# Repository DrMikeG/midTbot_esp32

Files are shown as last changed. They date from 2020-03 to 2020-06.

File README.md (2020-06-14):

# MidTBot ESP32



The MidTBot is a small and simple little pen plotter. All of the custom parts are 3D printed. The rest of the parts are low cost and easy to get.

The controller uses an ESP32 running Grbl_ESP32 firmware. It can be controlled via USB, Bluetooth or Wifi. You can simply upload gcode files to the unboard SD card and print.

The machine is controlled by a unique H-bot configuration, that uses a single belt. Two small stepper motors drive that belt in a special way to move in the X/Y plane. The pen is lifted by a hobby servo using a very simple and accurate mechanism.

[Here is a link to a video of the plotter in action.](https://www.youtube.com/watch?v=jiwWCrCfXrY)

The project is open source (Creative commons 4.0 Attribution - Share Alike) and all the files are in this Githob repo. Assembly instructions [are here](https://github.com/bdring/midTbot_esp32/wiki/Assembly-Instructions). If you have questions, please ask them by opening an issue in this repo.

### Check it out on GrabCad

Click on image for interactive viewer in browser.

GrabCAD (https://workbench.grabcad.com/workbench/projects/gcj3zJAQexD3ve_8KkwymatyKXhCWnRs8TB5U1ojGxl3s4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)

### Kits

There currently are no full kits for sale. [Controller kits are available on Tindie](https://www.tindie.com/products/33366583/midtbot-esp32-v1-controller-kit/).

### Donation

This project represents a lot of work. Please consider a safe, secure and highly appreciated donation via the PayPal link below.



## 2020-02-21 ##

I've got the latest arduino ide updated
I've added the esp32 board manager as described here https://github.com/espressif/arduino-esp32/blob/master/docs/arduino-ide/boards_manager.md

I've not pulled the development repo of https://github.com/espressif/arduino-esp32 - hopefully I don't need to do that?

I've copied the libraries from grbl\libs as described here: https://github.com/bdring/Grbl_Esp32/wiki/Compiling-the-firmware
/Volumes/ExtData03_2TB/Users/mike/Documents/Arduino/libraries

I've set the board settings in Ardino IDE as described here: https://github.com/bdring/Grbl_Esp32/wiki/Compiling-the-firmware

I've opened /Volumes/ExtData03_2TB/Users/mike/arduino/Grbl_Esp32/Grbl_Esp32/Grbl_Esp32.ino and I'm  trying to compile

Compiled unchanged...

The file "cpu_map.h" contains pin maps for several common setups. The master configuration file "config.h" selects one of those pin maps via a "#define" line near the top of that file.

Trying to program CPU_MAP_TEST_DRIVE onto actual board...

Compiled board with test_drive and that seemed to work.
Can't catch IP address on serial, but did find wifi GRBL_ESP, with password 12345678.
(See https://github.com/bdring/Grbl_Esp32/wiki/ESP3D-Web-UI-for-Grbl_ESP32)

You can also get them by sending $I on a serial terminal.

Changed config.h to have:
#define CPU_MAP_MIDTBOT // these are defined in cpu_map.h
recompiled and flashed to board.

Connected to the wifi network. Uploaded index.html.gz from this repo.

Putting esp board onto controller board
(Micro usb slot points off the edge of the board)

Plugged in stepper motor nearest boards (X?) Used UI to Jog X - it moves...
Connected second stepper - they both move when you job X/Y - remember it's a H-bot.

Connected up the servo. Jogged Z. That moves ok too.

Need to remember to adjust the stepper power to get the right cooking temp....

# 28th Feb 2020 #

Final screws arrived so attached steppers to the main board.
Threaded belt. Booted.

Need to follow instructions for attaching servo horn.

## Setting up the motors ##

Set the trimpot to minimum to start with, by turning the trimpot fully anti-clockwise. Turn clockwise until the motors are not skipping steps at your target speed and load.

https://github.com/bdring/midTbot_esp32/wiki/Setting-Up-the-Motors

https://github.com/bdring/midTbot_esp32/wiki/Setting-Up-the-Motors#overview-1

Set $rst=$ to reset all of the default Grbl settings.
Check the status by sending the ? character.
It should report that there is an alarm. This is because you have not homed yet.
Send $X to clear the alarm

Send $X to clear the alarm. You then need to send some small test moves to check the direction. 
Send G91 to put it in (incremental distance mode). Next send G0X2 to move the X axis 2mm to the right. Send G0Y2 to move the Y axis 2mm back. If either of these go the wrong direction you have to rotate one or more of the motor connectors 180 degrees.

Send $H to home the machine.

I think the wiring was correct all along - I just had one or more of the stepper drivers dialled down too low for homing work.
I cleared the alarm with $X, turned both trim pots a fraction clock-wise and rehomed in Y and X. Seemed fine so powered down for tonight.

For my colour wires, the correct wiring colours away from the ESP board are RGBY/GPBW
Wrong! Today the correct colours are: RGBY/WBPG

## Setting the X,Y 0,0 point.##
Homing does not set a 0,0 point. You need to tell it where that is. 
Home is min(X),max(Y) (top left hand corner)
Typically you would want jog to the lower left point and the set the 0,0 there.
min(X),min(Y) (lower left hand corner)
After homing move the down in negative Y. Be sure you don't hit the limit of travel. If you do, re-home and try again. 
Once there, set the 0,0. There are also zeroing buttons near the jog panel in the GUI.

## Pen Servo Setup ##

// Required
$rst=#
$3=4 (reverse the Z direction) (Has this reversed X and Y?!)
$102=90 (short pen lower stroke)
G10L2P0Z-5 (Avoid grounding pen at home.)

G0Z5 is pen up.

Clear the homing alarm by sending $X over the serial port.
Next send $rst=#. This will reset any machine offsets that might be in memory.
Send G0Z5 the servo should move to one end of the travel.
You can see the other end of the travel by sending G0Z0.
Send G0Z5 again to move to the pen up position. The servo should be rotating clockwise to lift the pen and counterclockwise to lower it. 

I need to send $3=4 to reverse the Z direction
(Not all servos travel the same way. If yours is going the wrong way, send $3=4 to reverse the Z direction.)

With the machine at Z5, mount the servo horn in a position that holds up the pen lift part. You want it to be holding the pen up close to the max height, but there should be a little travel left.

Changing $102 (adjusts Z0) From default (100). Sending $102=90 add 10% towards Z5 (up))

Used G0Z0 to install pen

## Home and first draw ##
Using WebUI 

Jogged as far in -Y as I dare.
Not sure I hit the zeroing button in the UI? (It dropped the pen) 
G10L20P0X0Y0 

I've drawn to test drawings of midthead.gcode (both seem to finish with a long random line with the pend down?!)

Trying to debug random line on completion? 
https://ncviewer.com/ shows this isn't a g-line. It could either be the home command or part of the firmware?

Also homed X and Y independently from Z? This stopped the pen dropping.
Click the X and Y wheel cross not the co
## Process ##
[Position bad paper]
Power on
Connect to wifi (12345678)
$X (clear alarm)
G0Z0 (pen down)
[Fit pen]
G0Z5 (pen up)
G10L2P0Z-5 (Avoid grounding pen at home.)
[Position good paper]
Click home Y
Click home X
Move -Y by about -1000 to move to bottom left corner of range
Click zero X
Click zero Y
[Need to figure out drawing Csys from 0,0 process]
[Execute GCode to draw picture]

if gcode contains G28 you may wish to remove it? Just end on pen up!

## How to make GCode ##
https://youtu.be/bbe56S_O-uI

Open Inkscape
> Document Properties
>> Default UNITS mm
>> Units mm
>> Width 180 (plotter bed size)
>> Height 220 

Import image into inkscape
Scale
Goto path tab
> Trace bitmap
>> Update
>> Ok
>> Close
Delete image (keep path)
Select object, on path menu click on object to path
>> Path tab
>>> Dynamic offset

/Volumes/ExtData03_2TB/Users/mik

## Added inkscape MakerBot Unicorn G-Code extension ##

Test params:
50/30/150/150/1500/1000/0/0 

https://shopcraftables.com/free-svg-cut-files/?sort=featured&page=6

## Messing about ##

There are some scaling tricks in inkscape.
Display units must be px.
Page scale should be 1.0

The produced gcode has F speed tags. Which can be removed or changed.

# 7th March 2020

https://www.norwegiancreations.com/2015/08/an-intro-to-g-code-and-how-to-generate-it-using-inkscape/

Useful guide to the inkscape gcode plugin. Recomends visualising (including timings) in Camotics

I probably don't need a post processor if I change the settings in the green tool table.

Having scolded my Son repeatedly about running with his tablet, he sheepishly presented me with broken headphones.

Dodgy jack? Easy repair? Only got to solder three wires - easy!

Not when they are crappy, enameled strand twisted pairs in a stretchy yellow plastic sleeve.

I only recently learned you can tin enamelled ends by bubbling them in solder.

After three fails attempts to splice them end-to-end with no strain relief, I admitted default and soldered them back to back.
At least my Son has his headphones back for (home) school tomorrow.

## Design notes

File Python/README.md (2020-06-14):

# Python processing

https://confluence.atlassian.com/bitbucketserver/markdown-syntax-guide-776639995.html

## 7th May 2020 ##

Read the file line by line

My file contains two layers, which are represented as groups <g> tags - this allows me to compare the edited and unedited porition - although my clumbsy edited actually edits both sections, and I use cut and paste to 'fix' one to be unedited afterwards.

Paths look like this.
The m is move to, 
the little c means this is a relative, polybezier.
the z at the end means closed
there are a few with h or v in, which is something I don't copy with yet.

To start with, I just counted the , but smaller area paths can still have high complexity
Then I tried to count the maxium displacement - this worked ok, but favoured long thing over round areas
Then I tried to estimate the area, treating the coordinates as vertices - this works pretty well, but makes some mistakes I don't yet understand

I am going to try and do a better approximation.

Example from round_church

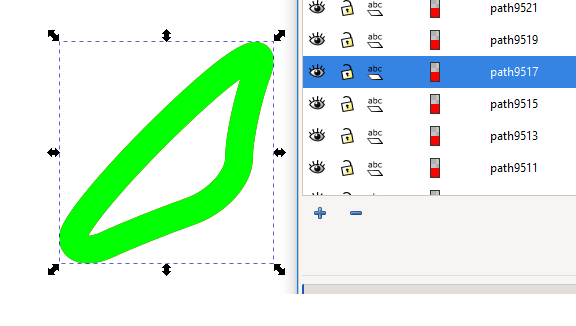
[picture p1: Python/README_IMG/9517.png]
Path 9517


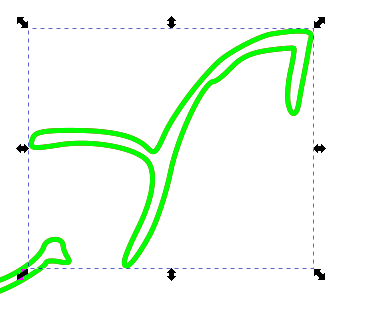
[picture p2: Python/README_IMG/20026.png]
Path 20026


<path
       style="fill:none;stroke:#ff0000;stroke-width:4.75441"
       d="m 4644.4095,-2548.3896 c 0,-3.5888
       5.4618,-17.2226
       12.1128,-30.2972 
       16.7193,-32.8657 
       19.9951,-59.5102 
       8.5584,-69.6047 
       -13.504,-11.9192 
       -53.5095,-18.6102 
       -83.053,-13.8908 
       -28.3172,4.5236 
       -30.4106,3.9963 -26.3313,-6.6333 2.1808,-5.684 10.6209,-7.3367 37.4652,-7.3367 38.9853,0 61.8412,5.1796 73.2651,16.6034 7.1663,7.1665 8.4357,6.2244 16.8068,-12.4727 8.8095,-19.6765 33.7221,-53.1188 52.8358,-70.926 10.1483,-9.4546 39.2933,-24.6833 50.9526,-26.6237 28.2093,-4.6946 40.3298,-3.7252 38.5725,3.0851 -1.0117,3.9224 -2.2978,10.3409 -2.8578,14.2633 -0.5601,3.9224 -2.5303,14.6198 -4.3793,23.7721 -1.8485,9.1522 -3.8882,20.3226 -4.5319,24.823 -1.9417,13.5655 -7.1421,15.0562 -10.1878,2.9204 -1.5756,-6.2776 -0.7303,-20.9135 1.8785,-32.5243 2.6087,-11.6108 4.1434,-21.7105 3.4103,-22.4436 -0.7331,-0.7332 -11.8451,0.1022 -24.6935,1.8561 -16.9475,2.3136 -26.8206,6.886 -35.9652,16.6559 -6.9329,7.4068 -14.5038,13.4669 -16.8244,13.4669 -10.009,0 -34.8409,51.7177 -42.2316,87.9566 -4.2666,20.9194 -13.2477,48.2348 -19.9581,60.7007 -13.6166,25.2942 -24.877,37.373 -24.8441,26.6495 z"
       id="path20026" />

https://www.w3.org/TR/SVG/paths.html

The cubic Bézier commands are as follows:

| Command | Name | Parameters | Description |
| --- | ----- | --- | --- |
| C (absolute) c (relative) | curveto | (x1 y1 x2 y2 x y)+ | Draws a cubic Bézier curve from the current point to (x,y) using (x1,y1) as the control point at the beginning of the curve and (x2,y2) as the control point at the end of the curve. C (uppercase) indicates that absolute coordinates will follow; c (lowercase) indicates that relative coordinates will follow. Multiple sets of coordinates may be specified to draw a polybézier. At the end of the command, the new current point becomes the final (x,y) coordinate pair used in the polybézier. |

This was invaluable https://medium.com/@adrian_cooney/bezier-interpolation-13b68563313a

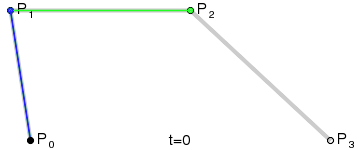
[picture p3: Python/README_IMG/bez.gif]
Cubic Bezier: How it work


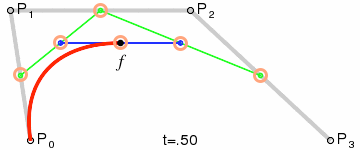
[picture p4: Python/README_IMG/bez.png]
Code for point at T


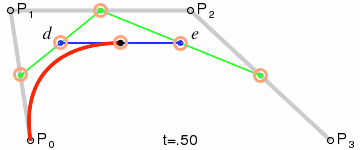
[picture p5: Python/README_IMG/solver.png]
solver


```
float T = 0.5;
CGPoint A = pointInLine(p0, p1, T);
CGPoint B = pointInLine(p1, p2, T);
CGPoint C = pointInLine(p2, p3, T);
CGPoint D = pointInLine(A, B, T);
CGPoint E = pointInLine(B, C, T);
CGPoint F = pointInLine(D, E, T); // The juicy one
```

4 pairs
start point, control point 1, control point 2 end point.
The curve passes though start and end point.

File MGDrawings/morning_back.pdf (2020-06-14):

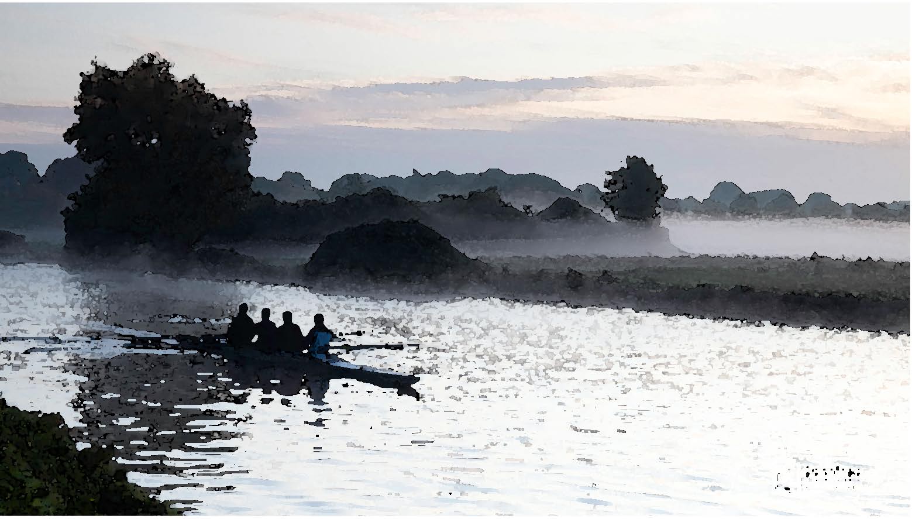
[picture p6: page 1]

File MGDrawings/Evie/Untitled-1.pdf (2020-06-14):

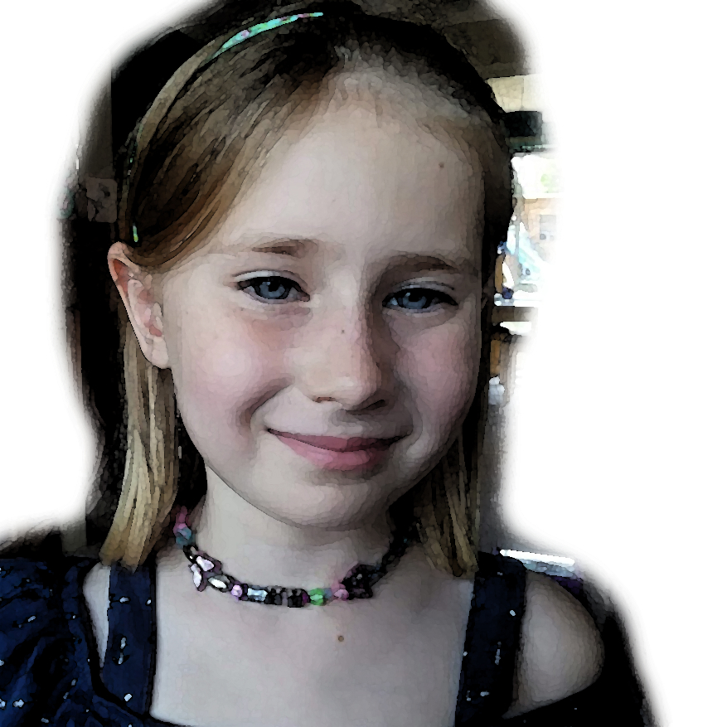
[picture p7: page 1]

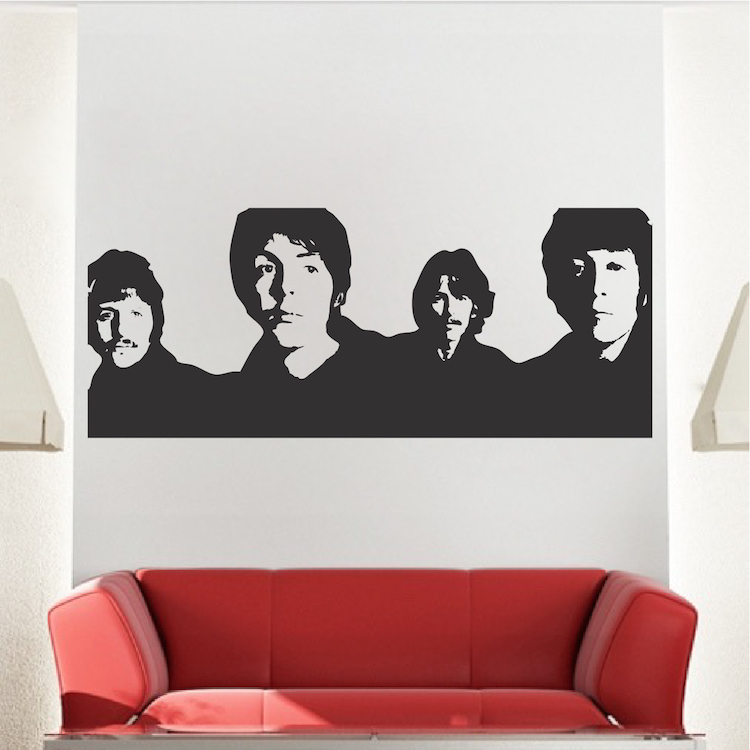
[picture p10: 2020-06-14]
MGDrawings/fab4/The_Beatles_Vinyl_Wall_Decal_Mural_Stickers_a87.jpg

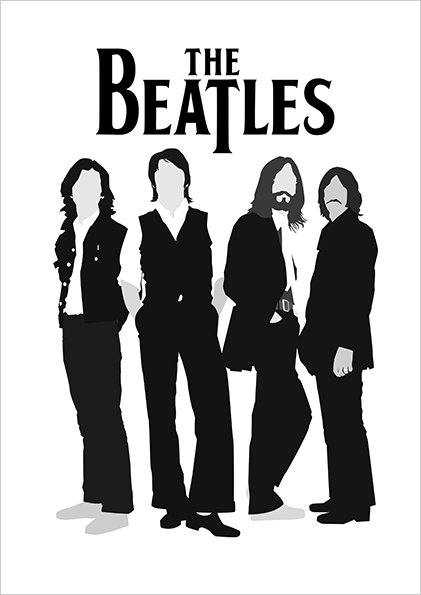
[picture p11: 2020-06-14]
MGDrawings/fab4/the-beatler1.png

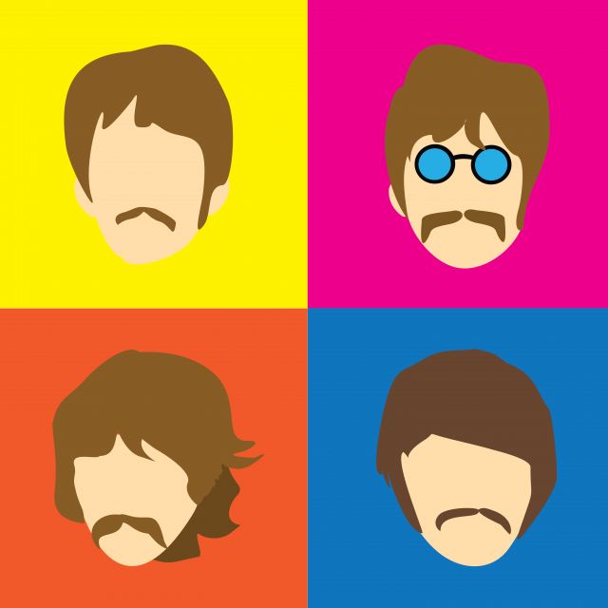
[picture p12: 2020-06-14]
MGDrawings/fab4/kPZz_WhzKAPGD-5CDNo-pWeygAgRfgy3-cropped-1x1-browser.jpg

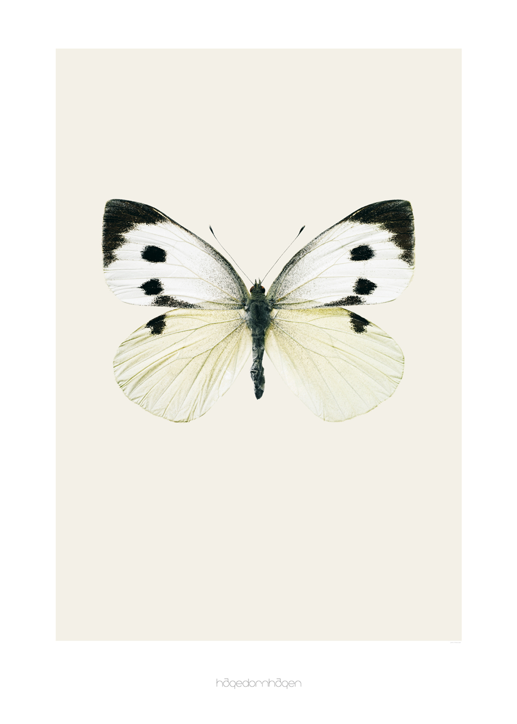
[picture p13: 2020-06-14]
MGDrawings/H-9.jpg

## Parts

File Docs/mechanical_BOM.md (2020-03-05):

### Mechanical Parts List

| Description | Qty  | Source | Help |
| --- | ---- | --- | --- |
| Carriage Block | 1 | 3D Printed |  Printed |
| Cover (optional) | 1 | 3D Printed |  Printed |
| Left Foot | 1 | 3D Printed |  Printed |
| Right Foot | 1 | 3D Printed |  Printed |
| Head Block | 1 | 3D Printed |  Printed |
| Tail Block | 1 | 3D Printed |  Printed |
| Pen Mounting Block | 1 | 3D Printed |  Printed |
| Linear Bearing Shaft 6mm Dia. x 200 lg. | 4 | [Amazon](<https://www.amazon.com/ReliaBot-inches-Hardened-Chrome-Plated/dp/B07R16DRVY>) |  Arrived |
| Linear Bearing LM6LUU (wide Style) | 4 | [Amazon](<https://www.amazon.com/uxcell-LM6LUU-6mmx12mmx35mm-Bushing-Bearing/dp/B01N3MO4FA>) | Arrived |
| Pulley GT2 16Tooth 6mm 5mm Shaft | 2 | [Amazon](<https://www.amazon.com/WINGONEER-Aluminum-Timing-Pulley-Printer/dp/B077YHJHVH>) |  5 Arrived |
| Smooth Idler Pulley 3mm I.D. 16Tooth Dia 13mm Flange Dia | 6 | [Amazon](<https://www.amazon.com/BALITENSEN-Smooth-Pulley-Toothless-Printer/dp/B077GXV7BJ>) | 10 Arrived [Issue](https://github.com/bdring/midTbot_esp32/issues/3) |
| Stepper Motor NEMA14 x 20mm Tall 5mm Shaft | 2 | [StepperOnLine](<https://www.omc-stepperonline.com/nema-14-stepper-motor/nema-14-bipolare-1-8deg-5ncm-7-08oz-in-0-4a-10v-35x35x20mm-4-fili.html>) |  2 Arrived [Issue](<https://github.com/bdring/midTbot_esp32/issues/10>) |
| GT2 6mm Wide Belt | 1m | [Amazon](<https://www.amazon.com/Mercurry-Meters-timing-Rostock-GT2-6mm/dp/B071K8HYB4>) | Arrived |
| Controller PCB | 1 | | Arrived |
| Button Screw M3 x 50mm | 1 | Ordered 2 Ebay (not arrived) Ordered 4 more from Kays (ebay) | |
| Hex Nut M3 Locking | 1 |  ordered 5 ebay |  arrived |
| Socket Head Screw M5 x 14 | 1 | ordered 5 ebay | arrived |
| Socket Head Screw M3 x 16 | 6 | ordered 10 ebay | arrived |
| Button Head Screw M3 x 8mm | 6 |  ordered 10 ebay (not arrived)  Ordered 10 more from Kays (6mm arrived - refunded) Order 10x10mm from Kays (ebay) | |
| Rubber Foot 1/2" dia x 1/8" Thk | 4 | [Amazon](<https://www.amazon.com/Self-Stick-Noise-Dampening-Bumpers-12-pieces/dp/B001WAK6DS>) | arrived |
| Bearing 3mm x 7mm x 3mm (683ZZ) | 2 | [Amazon](<https://www.amazon.com/gp/product/B00ZHSR2QU>) | Arrived |
| Hobby Servo MG90S | 1 | [Amazon](https://www.amazon.com/s?k=mg90) | Arrived |
| 12V 3A Power Supply | 1 | [Amazon](https://www.amazon.com/Adapter-100-240V-Transformers-Switching-Wireless/dp/B073WSWT34) |  In parts bin |

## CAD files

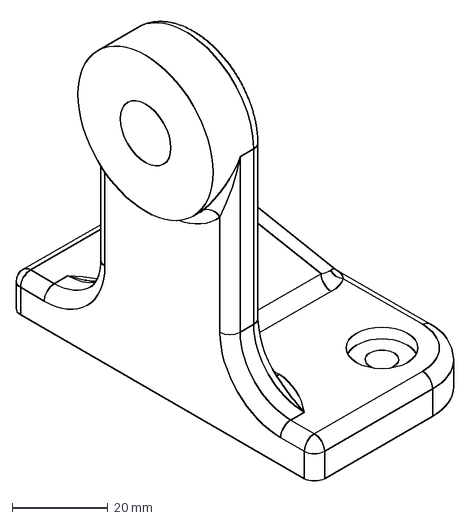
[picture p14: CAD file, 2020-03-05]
MGDrawings/New Stand_v20.dxf
91.5 x 97.3 mm

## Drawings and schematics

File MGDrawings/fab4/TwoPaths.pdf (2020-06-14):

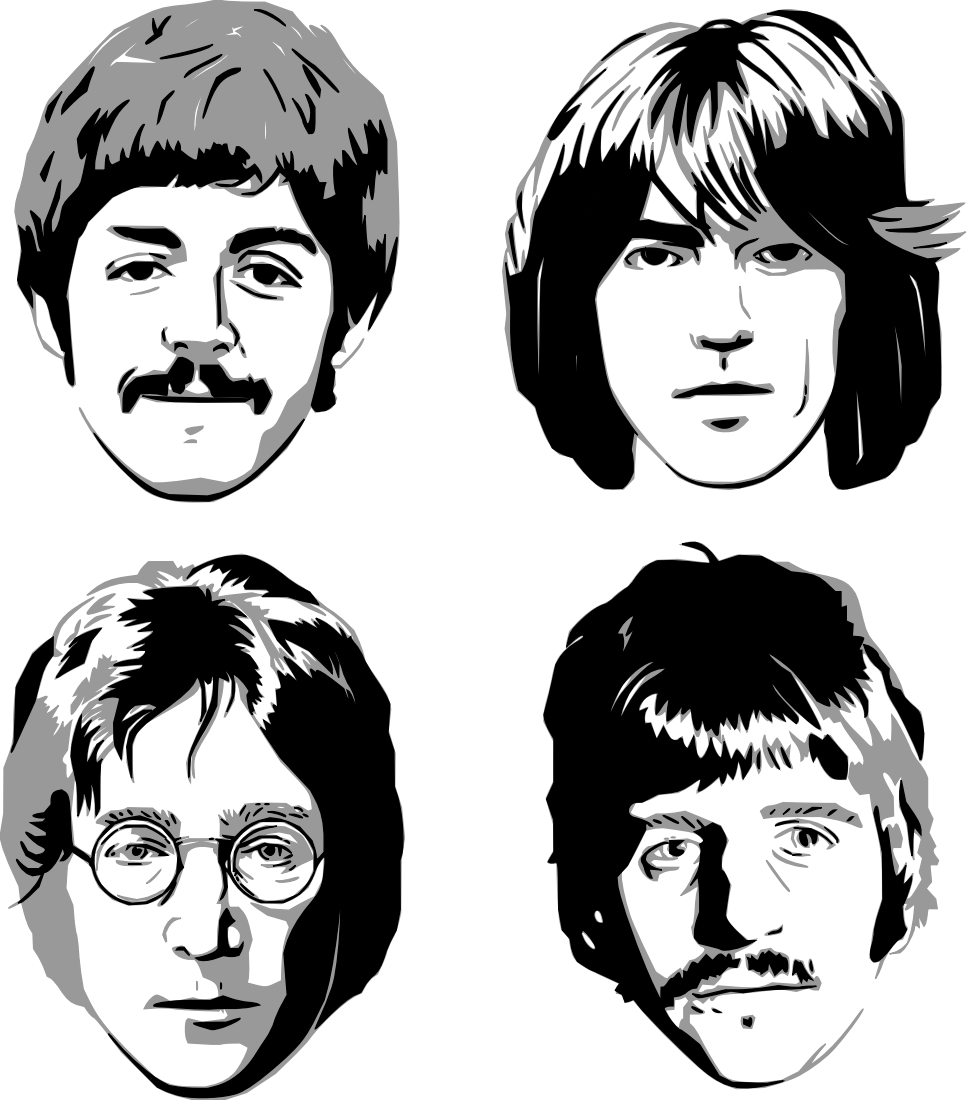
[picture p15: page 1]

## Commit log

2020-02-13 Stepper motors arrived
2020-02-14 recieved bearing shafts
2020-02-28 Homing X/Y and setting driver trim-pots
2020-03-02 More tests. First fast print
2020-03-05 more test images
    [New Stand_v20.dxf]
2020-05-07 Update round_church_two_paths_140x140.svg to have two layers, although I'm now only interested in the red layer
    Filtering out polygons with area less than 1600 - some of the things I am filtering look a bit odd?
2020-06-13 Added orchid picture
    [00_penDown.g, 01_penUp.g, 02_hold.g]
